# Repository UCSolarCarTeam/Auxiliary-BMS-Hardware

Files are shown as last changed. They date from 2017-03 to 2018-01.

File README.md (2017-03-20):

# Auxiliary-BMS-Hardware
Hardware for:
- Monitoring auxiliary battery voltage.
- Sending voltage status via CANbus.
- Controlling main battery contactor pre-charge/engagement.
- Monitoring pre-charge status, validating contactor engagement.
- Switching DC/DC-Converter source from auxiliary battery to main battery.

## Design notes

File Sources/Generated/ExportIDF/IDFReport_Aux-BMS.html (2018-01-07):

Altium customize

# IDF File Translation Report

Date: | | 2017-10-19
Time: | | 2:44:36 PM
Elapsed Time: | | 00:00:00
PCB Filename | : | C:\Users\giesbrecht\AppData\Local\Temp\Releases\Snapshot\3\Aux-BMS.PcbDoc
IDF Board Filename | : | C:\Users\giesbrecht\AppData\Local\Temp\Releases\Snapshot\3\Sources\Generated\ExportIDF\Aux-BMS.brd
IDF Library Filename | : | C:\Users\giesbrecht\AppData\Local\Temp\Releases\Snapshot\3\Sources\Generated\ExportIDF\Aux-BMS.pro

Errors

Back to top

Warnings

Back to top

Save Warnings

Back to top

Save Errors

Back to top

Export Warnings

Routing KeepOut with circle shape can not be exported.

Routing KeepOut with circle shape can not be exported.

Routing KeepOut with circle shape can not be exported.

Routing KeepOut with circle shape can not be exported.

Routing KeepOut with circle shape can not be exported.

Routing KeepOut with circle shape can not be exported.

Routing KeepOut with circle shape can not be exported.

Routing KeepOut with circle shape can not be exported.

Routing KeepOut with circle shape can not be exported.

Routing KeepOut with circle shape can not be exported.

Routing KeepOut with circle shape can not be exported.

Routing KeepOut with circle shape can not be exported.

Routing KeepOut with circle shape can not be exported.

Routing KeepOut with circle shape can not be exported.

Back to top

Export Errors

Back to top

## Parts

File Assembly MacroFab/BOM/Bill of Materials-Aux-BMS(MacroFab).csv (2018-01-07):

Comment | Description | Footprint | Designator | Quantity | Fitted | Manufacturer 1 | Manufacturer Part Number 1 | Supplier 1 | Supplier Part Number 1 | Supplier Unit Price 1 | Supplier Subtotal 1 | Supplier Currency 1
4-Pin Vertical Header |  | 4-Pin Vertical Header | P101 | 0 | Not Fitted
8 MHz | 8MHz ±30ppm 20pF Crystal | CRYSTAL_8MHZ | X100 | 0 | Not Fitted | Fox Electronics | FOXSLF/080-20 | Digi-Key | 631-1100-ND |  |  | USD
10K TRIM | TRIMMER 10K OHM 0.25W SMD | 10K_TRIM_SMD | R123 | 1 | Fitted | Nidec Copal | ST-4ETA-103 | Digikey | ST4ETA103CT-ND | 1.33 | 1.33 | USD
ADS7867 | ADC 10BIT 240KSPS SOT23-6 | SOT95P280X145-6N | U111 | 1 | Fitted | Texas Instruments | ADS7867IDBVT | Digi-Key | 296-18217-1-ND | 2.70 | 2.7 | USD
AP331A | Single Channel Comparator, Open Drain, SC-74A/SOT-753 | SOT95P285X130-5N | U108 | 1 | Fitted | Diodes | AP331AWG-7 | Digikey | AP331AWGDICT-ND | 0.35 | 0.35 | USD
Bourns TVS Diode 3.3V SOD323 | TVS DIODE 3.3VWM 10.9VC SOD323 | TVS Diode SOD-323 | D101, D104, D107, D108, D117 | 5 | Fitted | Bourns | CDSOD323-T03SC | Digi-Key | CDSOD323-T03SCCT-ND | 0.65 | 3.25 | USD
C006-T022U-00 | CAP TANT 1206 22uF 6.3V 2.5ohm 20% | Tantalum-1206 | C107 | 1 | Fitted | Nichicon | F930J226MAA | Digi-Key | 478-8164-1-ND | 0.34 | 0.34 | USD
C040-000U1-00 | CAP CER 0402 0.1uF 10V X5R 10% | CAPC1005X06N | C100, C101, C102, C105, C109, C110, C111, C112, C113, C114, C115, C118, C123, C124, C127, C128, C129, C131, C133, C135, C136 | 21 | Fitted
C040-0001N-00 | CAP CER 0402 1nF 50V X7R 10% | CAPC1005X06N | C125 | 1 | Fitted
C040-0010N-00 | CAP CER 0402 10nF 50V X7R 10% | CAPC1005X06N | C106 | 1 | Fitted
C040-0030P-00 | CAP CER 0402 30pF 25V NP0 5% | CAPC1005X06N | C120, C121 | 2 | Fitted
C060-0001U-00 | CAP CER 0603 1uF 16V X5R 20% | PCB_GENERIC_SMD_0603 | C116, C122, C134 | 3 | Fitted
C060-002U2-00 | CAP CER 0603 2.2uF 16V X5R 20% | PCB_GENERIC_SMD_0603 | C103, C104, C108, C117, C119, C126, C130, C132 | 8 | Fitted
D0S4-000CR-00 | LED 4SMD RGB 2Vf 3Vf 3Vf 20mA 10mA 10mA | CLMVB-FKA | D114 | 1 | Fitted | Cree | CLMVB-FKA-CFHEHLCBB7A363 | Digi-Key | CLMVB-FKA-CFHEHLCBB7A363CT-ND | 0.35 | 0.35 | USD
D060-000G2-00 | LED 0603 GREEN 3.2Vf 20mA | SMD_0603_LED | D1A, D1B, D1C, D1D, D2A, D2B, D2C, D2D, D106, D109, D112, D113 | 12 | Fitted | Wurth Electronics | 150060GS75000 | Digi-Key | 732-4971-1-ND | 0.14 | 1.68 | USD
D060-000R2-00 | LED 0603 RED 2Vf 20mA | SMD_0603_LED | D118 | 1 | Fitted | Wurth Electronics | 150060RS75000 | Digi-Key | 732-4978-1-ND | 0.14 | 0.14 | USD
FERRITE BEAD 0603 | Ferrite Bead, 0603, 600Ohm @ 100MHz, 200mOhm DC | INDC1608X10N | FB1A, FB1B, FB1C, FB1D, FB100, FB101 | 6 | Fitted | Bourns | MH1608-601Y | Digi-Key | MH1608-601YCT-ND | 0.10 | 0.6 | USD
FIDUCIAL | Alignment fiducial | FID08 | FID1, FID2, FID3, FID4, FID5 | 5 | Fitted
INFINEON BSC030P03NS3 G | P-Channel 30V 25.4A (Ta), 100A (Tc) 2.5W (Ta), 125W (Tc) Surface Mount PG-TDSON-8 | BSC030P03NS3 G | Q3A, Q3B, Q3C, Q3D, Q103 | 5 | Fitted | Infineon | BSC030P03NS3G | Digi-Key | BSC030P03NS3 GCT-ND | 1.77 | 8.85 | USD
LD2980CM33 | IC REG LDO 3.3V 50MA SOT23-5 | SOT95P280X145-5N | U106 | 1 | Fitted | STMicroelectronics | LD2980CM33TR | Digi-Key | 497-3479-1-ND | 0.57 | 0.57 | USD
LittleFuse_SP4021-01FTG-C | TVS DIODE 5VWM 19.6VC BI SOD323 | TVS Diode SOD-323 | D103, D105 | 2 | Fitted | Littelfuse | SP4021-01FTG-C | Digi-Key | F6273CT-ND | 0.65 | 1.3 | USD
MAX8212 |  | Maxim MAX8212 | U109 | 1 | Fitted | Maxim | MAX8212CSA+ | Digi-Key | MAX8212CSA+-ND | 4.81 | 4.81 | USD
MAX9923F | IC OPAMP CURR SENS 2.5KHZ 250V/V GAIN | TSSOP50P490X110-10N | U104 | 1 | Fitted | Maxim | MAX9923FEUB+ | Digi-Key | MAX9923FEUB+-ND | 2.26 | 2.26 | USD
Molex Ultrafit 3x1 | Molex Ultrafit 3x1 - 172310-1303 | Molex-Ultrafit-3x1 | P100, P104, P106 | 0 | Not Fitted
Molex Ultrafit 3x2 | Molex Ultrafit 3x2 - 172299-1206 | Molex-Ultrafit-3x2 | P1A, P1B, P1C, P1D | 0 | Not Fitted
NMOS - SSM3K333R | MOSFET N CH 30V 6A 2-3Z1A | NMOS - SSM3K333R - SOTFL95P180X88-3M | Q1A, Q1B, Q1C, Q1D, Q2A, Q2B, Q2C, Q2D, Q100, Q101, Q102 | 11 | Fitted | Toshiba | SSM3K333R,LF | Digi-Key | SSM3K333RLFDKR-ND | 0.402 | 4.422 | USD
ONSEMI_MBRM110LT1G | DIODE SCHOTTKY 10V 1A | ON Semi Schottky Diode - MBRM110LT1G | D110, D111 | 2 | Fitted | ON Semiconductor | MBRM110LT1G | Digi-Key | MBRM110LT1GOSDKR-ND | 0.45 | 0.9 | USD
ONSEMI_NL27WZ02 | 2CH 2IN NOR | TSSOP50P310X90-8N | U110, U112 | 2 | Fitted | ON Semiconductor | NL27WZ02USG | Digikey | NL27WZ02USGOSDKR-ND | 0.41 | 0.82 | USD
R060-00103-01 | RES 0603 10K 1% 100mW | PCB_GENERIC_SMD_0603 | R3A, R3B, R3C, R3D, R100, R102, R107, R110, R113, R114, R115, R116, R126, R130, R134 | 15 | Fitted
R060-00104-05 | RES 0603 100K 5% 63mW | PCB_GENERIC_SMD_0603 | R4A, R4B, R4C, R4D, R5A, R5B, R5C, R5D, R7A, R7B, R7C, R7D, R104, R106, R108, R111, R120, R124, R125, R127, R128 | 21 | Fitted
R060-00121-05 | RES 0603 120ohm 5% 63mW | PCB_GENERIC_SMD_0603 | R103 | 0 | Not Fitted
R060-00141-05 | RES 0603 140ohm 5% 63mW | PCB_GENERIC_SMD_0603 | R6A, R6B, R6C, R6D, R119, R121, R129 | 7 | Fitted
R060-00300-05 | RES 0603 30ohm 5% 100mW | PCB_GENERIC_SMD_0603 | R117, R118 | 2 | Fitted
R060-00331-05 | RES 0603 330ohm 5% 63mW | PCB_GENERIC_SMD_0603 | R1A, R1B, R1C, R1D, R2A, R2B, R2C, R2D, R101, R105, R109, R112, R131 | 13 | Fitted
R060-00823-01 | RES 0603 82K 1% 100mW | PCB_GENERIC_SMD_0603 | R133 | 1 | Fitted
R060-03572-01 | RES 0603 35.7K 1% 100mW | PCB_GENERIC_SMD_0603 | R132 | 1 | Fitted
R78E-1.0 DC/DC |  | R78-1.0 | U100 | 0 | Not Fitted
resistor_sense_1mOhm_2512 | 1mOhm Current Sense | RESC6432X11N | R122 | 1 | Fitted | Panasonic ECG | ERJ-M1WTF1M0U | Digi-Key | P1.0NDCT-ND | 0.55 | 0.55 | USD
RT9818C-29GV | IC VOLT DETECTOR 2.9V SOT23-3 | SOT95P279X129-3N | U107 | 1 | Fitted | Richtek | RT9818C-29GV | Digi-Key | 1028-1020-1-ND | 0.40 | 0.4 | USD
SCH_MLX_1X2 |  | PCB_MLX_MICROFIT_1X2 | P105 | 0 | Not Fitted
SCH_MLX_MICROFIT_3X2 |  | PCB_MLX_MICROFIT_3X2 | P102, P103 | 0 | Not Fitted
Si8631AB-B-IS1 | 2/1 Channel Digital Isolator | SOIC127P600X175-16N | U105 | 1 | Fitted | Silicon Labs | Si8631AB-B-IS1 | Digi-Key | SI8631AB-B-IS1-ND | 1.40 | 1.4 | USD
SMT, shrouded | ARM Cortex-M 10pin connector,shrouded,SMT | CONN-50mil-10POS-SMD | J100 | 1 | Fitted | CNC Tech | 3220-10-0300-00 | Digi-Key | 1175-1629-ND | 0.61 | 0.61 | USD
SN65HVD1050DR | IC EMC CAN TRANSCEIVER 8-SOIC | SOIC127P600X175-8N | U101 | 1 | Fitted | Texas Instruments | SN65HVD1050DR | Digi-Key | 296-26335-1-ND | 1.22 | 1.22 | USD
SPST-NO Solid State Relay | SPST-NO Solid State Relay | SPST-NO Solid State Relay - IXYS | K100 | 1 | Fitted
STM32F407VGT6 | ARM Cortex-M4 32-bit MCU+FPU, 210 DMIPS, 1024 kB Flash, 192 kB Internal RAM, 82 I/Os, 100-pin LQFP, -40 to 85 degC, Tray | STM-LQFP100_N | U103 | 1 | Fitted | STMicroelectronics | STM32F407VGT6 | Digi-Key | 497-11605-ND | 12.74 | 12.74 | USD
Tactile Switch |  | C&K 4 pin Tactile Switch | S100, S101, S102 | 3 | Fitted | ITT C&K | PTS645SH50SMTR92LFS | Digi-Key | CKN9085CT-ND | 0.21 | 0.63 | USD
TI_SN74LV08A | AND GATE 4CH 2IN SOIC14 | SOIC127P600X175-14N | U113 | 1 | Fitted | Texas Instruments | SN74LV08ADR | Digikey | 296-26531-6-ND | 0.36 | 0.36 | USD
TPS73733DRV | IC REG LDO 3.3V 1A 6SON | SON65P200X80_HS-7M | U102 | 1 | Fitted | Texas Instruments | TPS73733DRVR | Digikey | 296-40960-1-ND | 1.59 | 1.59 | USD
TVS_14V_UNI | TVS DIODE 14VWM 23.2VC SMF | SODFL370X108-2N | D3A, D3B, D3C, D3D, D4A, D4B, D4C, D4D, D100, D102, D115, D116, D119 | 13 | Fitted | Vishay Semiconductors | SMF14A-E3-08 | Digi-Key | SMF14A-E3-08GICT-ND | 0.363 | 4.719 | USD
X-Out/Skip Mark | X-Out/Skip Mark for bad board/do not populate | SKIP20-NOCOPPER | SKIP1 | 0 | Not Fitted

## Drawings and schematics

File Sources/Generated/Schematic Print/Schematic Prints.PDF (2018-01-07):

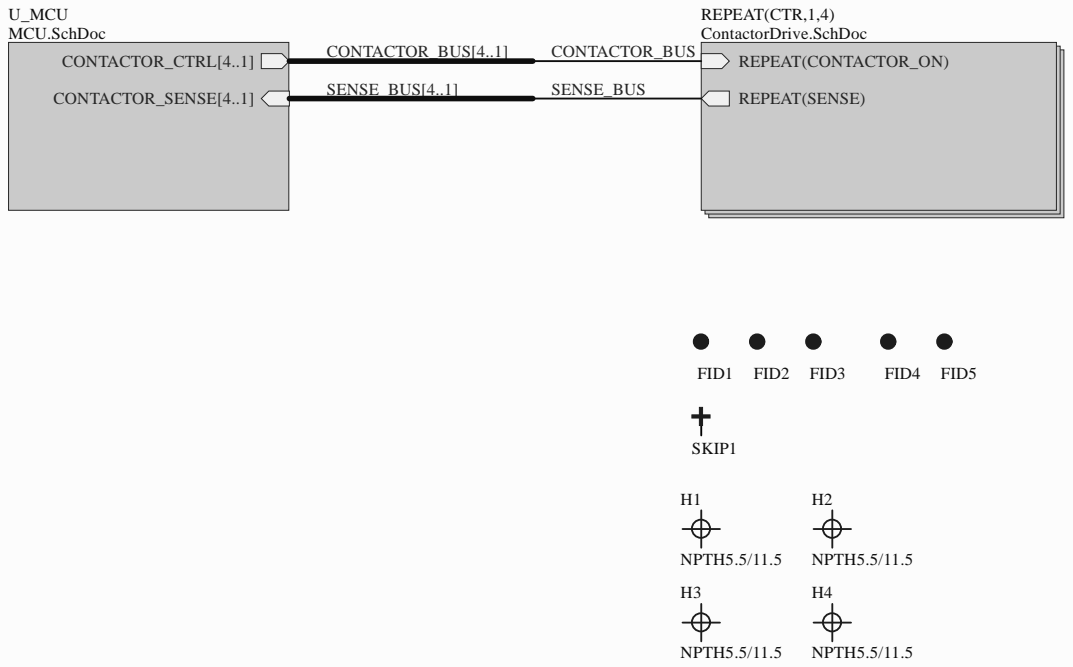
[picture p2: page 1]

Main Title | UofC Solar Car Team

Size: D | Number: N/A | Revision: 1
Drawn By: DSG | Date: 2017-10-19 | Sheet of

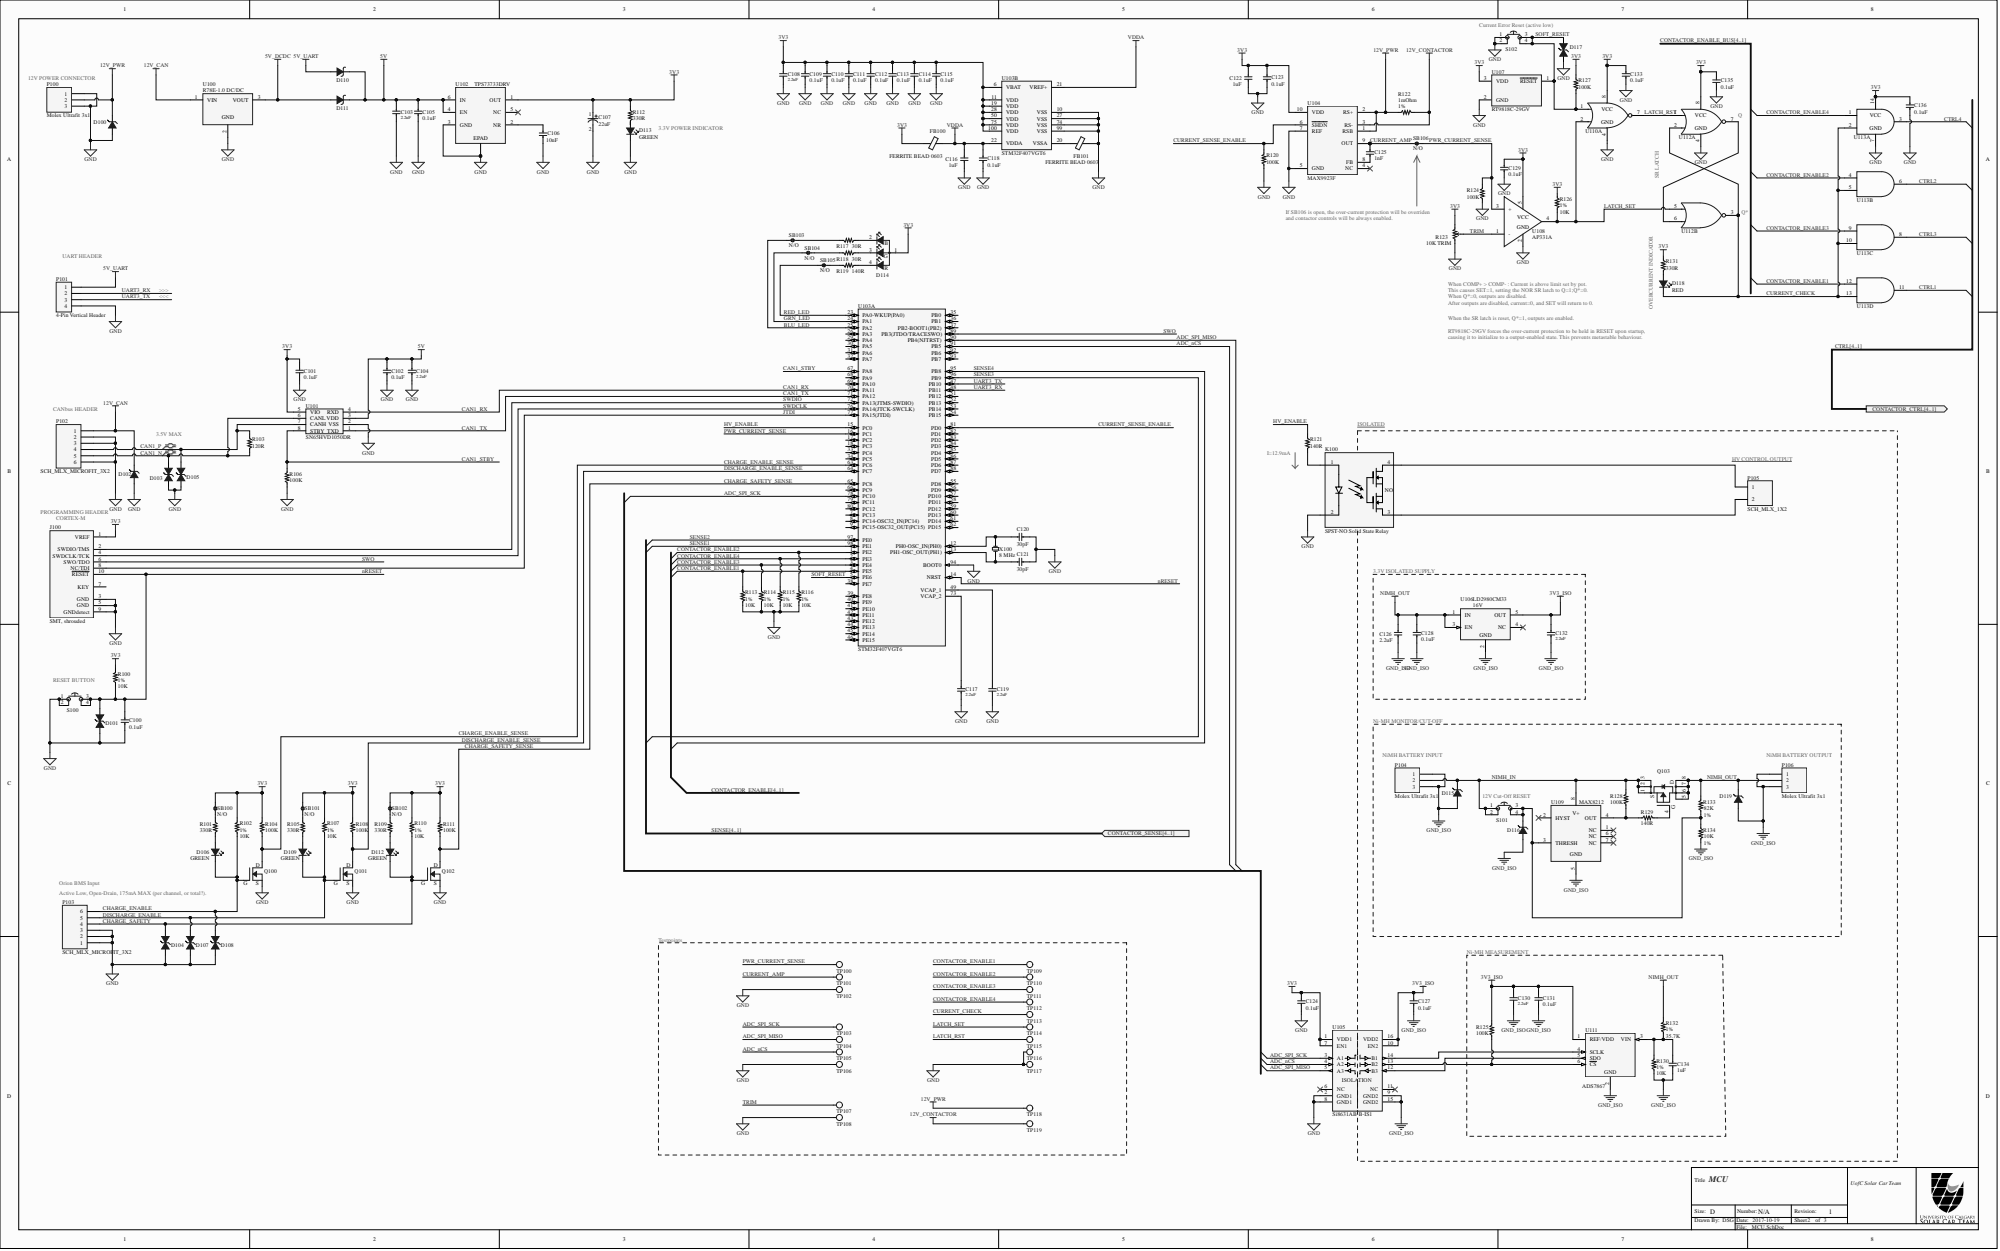
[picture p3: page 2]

Current Error Reset (active low)

If SB106 is open, the over-current protection will be overriden
and contactor controls will be always enabled.

When COMP+ > COMP- : Current is above limit set by pot.
This causes SET=1, setting the NOR SR latch to Q=1;Q*=0.
When Q*=0, outputs are disabled.
After outputs are disabled, current=0, and SET will return to 0.

When the SR latch is reset, Q*=1, outputs are enabled.

RT9818C-29GV forces the over-current protection to be held in RESET upon startup,
causing it to initialize to a output-enabled state. This prevents metastable behaviour.

SPST-NO Solid State Relay

SENSE1 | PE1 98 PH0-OSC_IN(PH0) PH1-OSC_OUT(PH1) BOOT0 NRST VCAP_1 | 12 | X100

CONTACTOR_ENABLE4 | | | PE3 2 | 94
CONTACTOR_ENABLE3 | | | PE4 3
CONTACTOR_ENABLE1 | | PE5 4 | 14

49 | GND | nRESET

Ni-MH MONITOR/CUT-OFF

Orion BMS Input
Active Low, Open-Drain, 175mA MAX (per channel, or total?).

CHARGE_ENABLE
DISCHARGE_ENABLE
CHARGE_SAFETY

VDD1 1 | NC

GND GND 12V_PWR TP107 TP118 TP119 GND | ISOLATION

UofC Solar Car Team

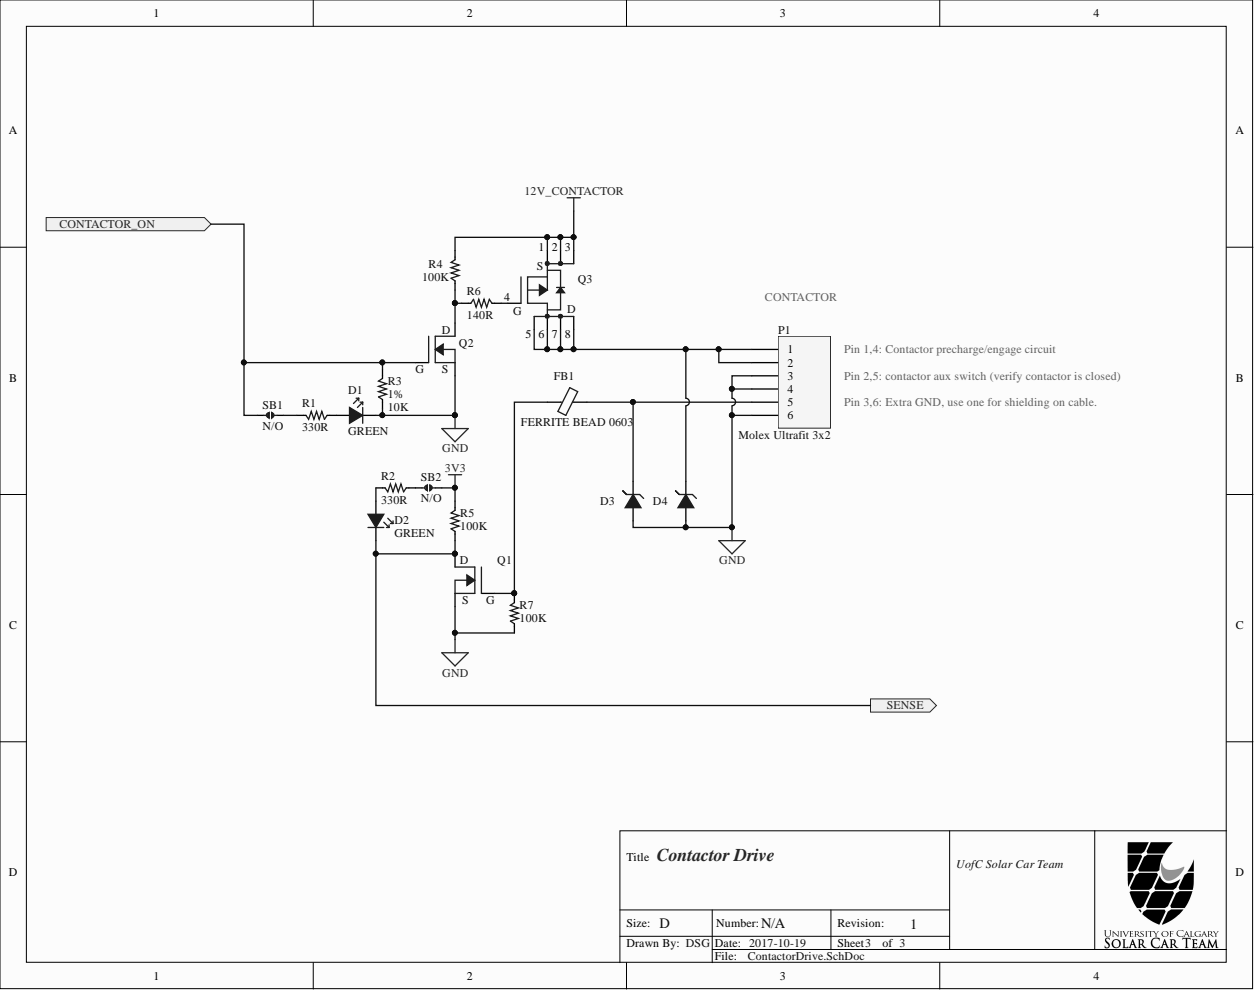
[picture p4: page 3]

Pin 1,4: Contactor precharge/engage circuit

Pin 2,5: contactor aux switch (verify contactor is closed)

Pin 3,6: Extra GND, use one for shielding on cable.

UofC Solar Car Team

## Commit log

2016-08-20 Reformatted file folders.
    [Auxiliary-BMS_master.PrjPcb, Connectors.SchDoc, MCU.SchDoc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]
2016-08-29 Added project files for 32QFN and 32TQFP breakout.
    [breakout_32QFN-32TQFP.PcbDoc, breakout_32QFN-32TQFP.PrjPcb, breakout_32QFN-32TQFP.SchDoc]
2016-08-29 Finish breakout, create panel.
    [breakout_32QFN-32TQFP.PcbDoc, breakout_32QFN-32TQFP.PrjPcb, panel.PcbDoc]
2016-08-31 Cleaned up top layer routing.
    [breakout_32QFN-32TQFP.PcbDoc, breakout_32QFN-32TQFP.PrjPcb]
2016-08-31 Supplier package; contains gerber files and NC drill file. readme.txt describes gerber generation.
2016-08-31 Re-exported package - small silkscreen change.
2016-08-31 Small silkscreen change.
    [breakout_32QFN-32TQFP.PcbDoc, breakout_32QFN-32TQFP.PrjPcb]
2018-01-07 Release PCB version 1, revision 1
    [0603-FERRITE-600Ohm.PcbLib, 0603-FERRITE-600Ohm.SchLib, 2 Pin 100 mil Right Angle Header - Surface Mount.PcbLib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]
